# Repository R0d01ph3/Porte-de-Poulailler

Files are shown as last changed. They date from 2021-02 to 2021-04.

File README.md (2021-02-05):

# Porte de poulailler

## Fonctionnement
Pour fixer l'heure sur la rtc : https://github.com/NorthernWidget/DS3231

En fonction de la date et l'heure la porte du poulailer s'ouvre et se ferme.

La porte est un systeme pont levis avec une poulie

Pour la fermeture le moteur s'enclenche pour enrouler le fil.  
Dés que la porte touche le capteur de fin de course (positionné sur la butée de la porte) il doit s'arreter.  
Finalement j'ai choisi de lancer une premiere fermeture puis ouvrir pendant une seconde et relancer une fermeture.  
Ceci car je me suis rendu compte que parfois la porte se bloquait un peu avant le capteur de fin de course.  

Pour l'ouverture j'avais mis le même systeme que la fermeture avec le capteur de butée sous la porte.  
Mais comme les poules marchent régulièrement sur la porte le capteur a fini par se casser et il était détecté tout le temps ouvert.  
J'ai donc utilisée une tempo (mesure du temps moyen d'ouverture de la porte plus petite rallonge de fil de pêche) pour faire l'ouverture.  

## requirements
Logiciel
- arduino pour coder et téléverser sur l'arduino

Librairies 
- DS3231.h cf https://github.com/NorthernWidget/DS3231
- Wire.h cf https://www.arduino.cc/en/reference/wire

## Materiel
- un arduino nano (type elegoo)
- une rtc DS3231
- un moteur dc (aliexpress https://fr.aliexpress.com/item/4000295013680.html?spm=a2g0s.9042311.0.0.27426c37luoqCs)
- une alim 12v
- un pont L298N pour controller le moteur
- 2 boutons poussoirs
- 1 capteur fin de course (style relai)
- des cables du pont et autres
- un fer à souder et de quoi souder
- poulie
- fil de peche pour la traction de la porte
- charniere pour la porte
- crochet pour relier le fil au moteur
- une boite de derivation pour mettre tous les composants à l'abri de la pluie et des poules

## Cablage
Voir fritzing ou image

## Code
Voir fichier .ino

## Amélioration
remplacer les boutons poussoirs par un module wifi ESP8266 flashé tasmota pour pouvoir piloter la porte via un smartphone
cf https://github.com/R0d01ph3/Porte-Poulailler-wifi

## Sources
Je me suis inspiré de beaucoup de sites différents.  
J'en oublies surement beaucoup mais voilà quelques sources :

- https://electrotoile.eu/fabrication-diy-porte-poulailler-automatique-arduino.php
- http://raspi.projets.free.fr/automatisme-de-poulailler-connecte.html
- http://portepoulailler.unblog.fr/creer-votre-porte-de-poulailler-pour-12e/
- https://journaldunarchiviste.fr/2019/01/04/domotique-poulailler-connecte-partie-1/

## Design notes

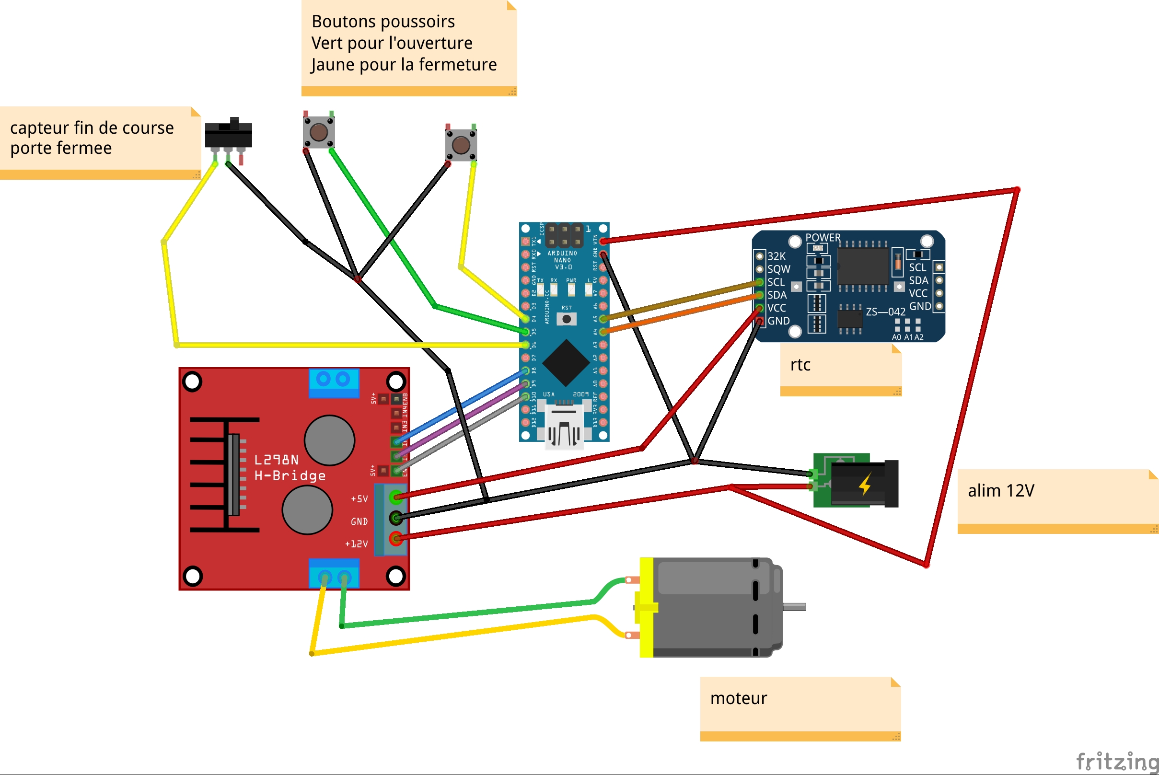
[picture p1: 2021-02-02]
porte_poulailler_v2_bb.jpg

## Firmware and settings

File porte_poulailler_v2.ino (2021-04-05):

#include <Wire.h>//https://www.arduino.cc/en/reference/wire
#include <DS3231.h>//https://github.com/NorthernWidget/DS3231

//RTC
RTClib RTC;

int commande_haut = 4; // Déclaration broche Bouton fermeture
int commande_bas = 5; // Déclaration broche Bouton ouverture
int fin_de_course_haut = 6; // Capteur fin de course haut (porte fermée)
int enA = 10;                   // crée une variable de type "int", nommée "enA" et attachée à la Broche 10, qui permet de gérer la vitesse du moteur.
int in1 = 9;                    // crée une variable de type "int", nommée "in1" et attachée à la Broche 9, qui permet de gérer le sens de rotation.
int in2 = 8;                    // crée une variable de type "int", nommée "in2" et attachée à la Broche 8, qui permet de gérer l'autre sens de rotation.

unsigned long debut_fermeture; // timer pour debut de fermeture
unsigned long timeoutMoteur = 30000; // timeout ou on considere le moteur bloquee
int delayTime = 10; // Temps entre chaque pas 10ms
boolean fdch = false; // Déclaration variable Fin de Course Haut (porte fermee)
boolean etat_bp_h = false, etat_bp_b = false; // Déclaration des variables bas et haut
boolean mem_h = false, mem_b = false, mem_fdch = false; // Déclaration des mémoires


// tableau des horaires selon les quinzaines
// tableau des horaires marche 2 mois par 2 mois (janvier avec decembre, février avec novembre, ...)
// il fonctionne par 15aine
// janvier du 01 au 15 correspond a l'index 0, janvier du 16 au 31 correspond à l'index 1
// décembre du 01 au 15 correspond a l'index 1, décembre du 16 au 30 correspond a l'index 0
// ...
int LeveSoleilHeure[12]= {7,7, 7,7, 6,6, 5,5, 5,5, 5,5 };   
int LeveSoleilMinute[12]= {15,15, 0,0, 45,45, 30,30, 15,15, 0,0 };   
int CoucheSoleilHeure[12]= {19,19, 19,19, 20,20, 20,20, 21,21, 21,21 };   
int CoucheSoleilMinute[12]={15,15, 30,30, 0,0, 30,30, 0,0, 30,30 }; 
  
void setup() {
  Serial.begin(9600); // Ouverture du port série et debit de communication fixé à 9600 bauds
  Wire.begin();
  pinMode(commande_haut, INPUT_PULLUP); // Déclaration entrée pull-up sur entrée BP haut
  pinMode(commande_bas, INPUT_PULLUP); // Déclaration entrée pull-up sur entrée BP bas
  pinMode(fin_de_course_haut, INPUT_PULLUP); // Déclaration entrée pull-up sur entrée Fin de course haut
  pinMode(enA, OUTPUT);         // indique que la broche de la variable "enA" donc ici la PIN 10, est une sortie.
  pinMode(in1, OUTPUT);         // indique que la broche de la variable "in1" donc ici la PIN 9, est une sortie.
  pinMode(in2, OUTPUT);         // indique que la broche de la variable "in2" donc ici la PIN 8, est une sortie.
  etat_bp_h = !digitalRead(commande_haut); // Inverse de la lecture sur entrée BP haut
  etat_bp_b = !digitalRead(commande_bas); // Inverse de la lecture sur entrée BP bas
  fdch = !digitalRead(fin_de_course_haut); // Inverse de la lecture sur entrée Fin de course haut
  mem_fdch = fdch; // Mémorisation du nouvel état du fin de course bas
  mem_h = etat_bp_h; // Mémorisation du nouvel état du bouton haut
  mem_b = etat_bp_b; // Mémorisation du nouvel état du bouton bas
  DateTime now = RTC.now(); //  Utile au debug pour connaitre l'heure au debut du programme
  Serial.println(now.hour()); // heure
  Serial.println(now.minute()); // minute
}


void loop() {
  etat_bp_h = !digitalRead(commande_haut); // Inverse de la lecture sur entrée BP haut
  etat_bp_b = !digitalRead(commande_bas); // Inverse de la lecture sur entrée BP bas
  fdch = !digitalRead(fin_de_course_haut); // Inverse de la lecture sur entrée Fin de course haut
  DateTime now = RTC.now();   // recupere la date
  int index= getIndex(now); // calcul de l'index pour le tableau des horaires

  //debug
  if (fdch != mem_fdch) // Changement d'état du fin de course haut (front montant ou descendant)
  {
    if (fdch) 
    {
      Serial.println("Porte fermée !"); // Affichage sur le moniteur série du texte
    }
    if (!fdch)
    {
      Serial.println("Porte non fermée"); // Affichage sur le moniteur série du texte
    }
  }
  mem_fdch = fdch; // Mémorisation du nouvel état du fin de course bas
  
  if (etat_bp_h != mem_h) // Changement d'état du bouton poussoir haut (front montant ou descendant)
  {
    if (etat_bp_h && !fdch) // Appui sur BP haut et la porte n'est pas fermee
    {
      Serial.println("Fermer");
      Fermer_porte(); // ferme
      Ouvrir_1sec(); // ouverture d'1 sec (utile car dans certains cas le fin de course n'était pas atteint)
      Fermer_porte(); //ferme
    }
  }
  mem_h = etat_bp_h; // Mémorisation du nouvel état du bouton haut
  
  if (etat_bp_b != mem_b) // Changement d'état du bouton poussoir bas (front montant ou descendant)
  {
    if (etat_bp_b && fdch) // Appui sur BP bas mais pas sur le haut
    {
      Serial.println("Ouvrir");
        Ouvrir_porte();
    }
  }
  mem_b = etat_bp_b; // Mémorisation du nouvel état du bouton bas

  // ouverture en fonction de l'heure
  if (canOpen(now, index)) //en horaire d'ouverture
  {
    Ouvrir_porte();;
  }
  //fermeture en fonction de l'heure et si la porte n'est pas deja fermee
  if (!fdch && canClose(now,index))//(fdcb && canClose(now,index)) //Porte non fermée et en horaire de fermeture
  {
    Fermer_porte();
    Ouvrir_1sec();
    Fermer_porte();
  }
}

void Ouvrir_1sec() {
    digitalWrite(in1,HIGH);       // met la broche in1 à l'état bas, la carte n'injecte pas d'électricité, le moteur ne tourne pas dans le sens de in1.
    digitalWrite(in2,LOW);      // envoie l'électricité dans la broche in2 (donc la PIN 8)ce qui fait donc tourner le moteur dans le sens de rotation de in2.
    analogWrite(enA,200);        // défini la vitesse du moteur, ici 200 sur un maximum de 255 (échélle comprise entre 0 et 255, car cela correspond à 8 bits soit 1 octet).
    delay(1000); // delay d'une seconde
    fdch = !digitalRead(fin_de_course_haut); // récuperation du fin de coursehaut
    Arret(); // arret de moteurs
}


void Fermer_porte() {
  debut_fermeture = millis(); // calcul du temps de fermeture
  while (!fdch) {
      digitalWrite(in1,LOW);       // met la broche in1 à l'état bas, la carte n'injecte pas d'électricité, le moteur ne tourne pas dans le sens de in1.
      digitalWrite(in2,HIGH);      // envoie l'électricité dans la broche in2 (donc la PIN 8)ce qui fait donc tourner le moteur dans le sens de rotation de in2.
      analogWrite(enA,200);        // défini la vitesse du moteur, ici 200 sur un maximum de 255 (échélle comprise entre 0 et 255, car cela correspond à 8 bits soit 1 octet).
      delay(delayTime);   // pas de 10ms

      fdch = !digitalRead(fin_de_course_haut); // récupere l'etat du fin de course
      etat_bp_b = !digitalRead(commande_bas); // Inverse de la lecture sur entrée BP bas
      if (fdch) // si porte fermee
      {
        Serial.println("Porte en haut"); // Affichage sur le moniteur série du texte
        Arret(); // arret des moteurs
        break; // fin
      }
      if ((millis() - debut_fermeture) > timeoutMoteur) {
        Serial.println("Porte bloquee");
          Arret(); // arret carte timeout atteint
          break;
        }
  }
}

void Ouvrir_porte() {
    digitalWrite(in1,HIGH);     // met la broche in1 à l'état bas, la carte n'injecte pas d'électricité, le moteur ne tourne pas dans le sens de in1.
    digitalWrite(in2,LOW);      // envoie l'électricité dans la broche in2 (donc la PIN 8)ce qui fait donc tourner le moteur dans le sens de rotation de in2.
    analogWrite(enA,200);       // défini la vitesse du moteur, ici 200 sur un maximum de 255 (échélle comprise entre 0 et 255, car cela correspond à 8 bits soit 1 octet).
    delay(16000);               // delay 16sec le temps d'ouverture de la porte
    fdch = !digitalRead(fin_de_course_haut); // récupère l'etat du relais porte fermée
    Arret();                    // arret du moteur
}


void Arret() {
  digitalWrite(in1,LOW);       // en mettant la broche in1 à l'état bas, la carte n'injecte pas d'électricité, le moteur est donc à l'arrêt.
  digitalWrite(in2,LOW);       // en mettant la broche in2 à l'état bas, la carte n'injecte pas d'électricité, le moteur est donc à l'arrêt.
}

int getIndex(DateTime t){
  int Index=t.month(); // on récupere le mois
  if (t.month()>6)     // si le mois est après Juin
  {
    Index=13-t.month();    //on récupère le 13 moins le mois (décembre est avec janvier, nomvembre avec fevrier , ...) 
    Index=(Index-1)*2;     // on fait -1 x 2 car le tableau est par quinzaine
    if( t.day()<15)       // si on est dans la quinzaine du début du moins on augmente l'index
    {
      Index++;   
    }
  }
  else   // mois avant juin
  {  
    Index=(Index-1)*2;     // on fait -1 x 2 car le tableau est par quinzaine
    if( t.day()>15)       // si on est dans la quinzaine de fin du moins on augmente l'index
    {
      Index++;   
    }
  }   
  return Index;   
}

boolean canOpen(DateTime t,int index)   
{ 
  if (t.hour()== LeveSoleilHeure[index] && t.minute()== LeveSoleilMinute[index] && t.second()==0 )
  {
    Serial.println("Can open");
    return true;
  }
  else    
  {
    return false;   
  }
}   

boolean canClose(DateTime t,int index)
{  
  if (t.hour()== CoucheSoleilHeure[index] && t.minute()== CoucheSoleilMinute[index] && t.second()==0 )
  {
    Serial.println("Can close");
    return true;   
  }
  else    
  {
    return false;   
  }
}   
